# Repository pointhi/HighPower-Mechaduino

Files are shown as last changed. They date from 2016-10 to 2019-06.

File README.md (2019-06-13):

View this project on [CADLAB.io](https://cadlab.io/project/1867). 

# HighPower-Mechaduino

KiCad based Mechaduino derivative which drives up to 10A.

This is the original Meachaduino Project: https://hackaday.io/project/11224-mechaduino

**Warning: This Board is currently under development. Simply fabricating it doesn't mean it would work!**
See [v0.1_BUILD_LOG.md](https://github.com/pointhi/HighPower-Mechaduino/blob/master/v0.1_BUILD_LOG.md) for some problems
found while building the first prototype.

A big thanks to the [Shuttleworth Foundation](https://shuttleworthfoundation.org) for supporting the development of this Project.

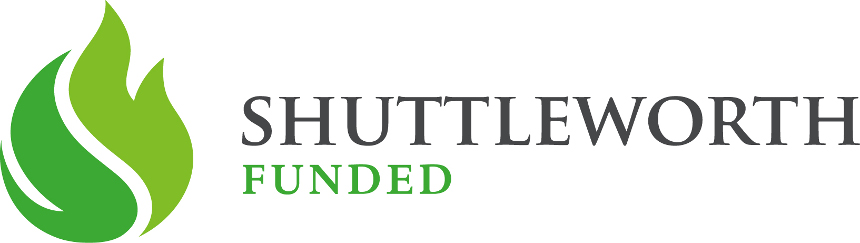
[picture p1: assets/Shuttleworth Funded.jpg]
Shuttleworth Funded


### Improvements

* ESD protection (especially USB)
* flyback diodes
* stronger drivers
* better silkscreen
* correct use of blocking capacitors
* fuse (for protection against polarity reversal and shorts)
* input voltage measurement
* supply of the microcontroller via the motor voltage supply
* external storage for calibration and configuration data
* Temperature sensor

### Planned Electrical/Mechanical Ratings

* Input Voltage-range of about 12V-50V
* N-Mosfet Driver which is capable of about 10A
* board in the size of NEMA 23 (56x56xmm) or NEMA 24 (60x60mm)

### Interfaces

* USB
* UART (3.3V)
* Step/Dir/Enable (PoStep25-32 Compatible)

### various informations

* [BOM](https://rawgit.com/pointhi/HighPower-Mechaduino/master/pcb/HighPower-Mechaduino.html) can be created using [KiBoM](https://github.com/SchrodingersGat/KiBoM)
* There exists a modified version of the Firmware for this project: [ElektronikNode/Mechaduino-Firmware](https://github.com/ElektronikNode/Mechaduino-Firmware)

## License

Hardware including documentation is licensed under [CERN OHL v.1.2. license](http://www.ohwr.org/licenses/cern-ohl/v1.2)

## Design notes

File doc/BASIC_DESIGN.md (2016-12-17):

## Basic Design

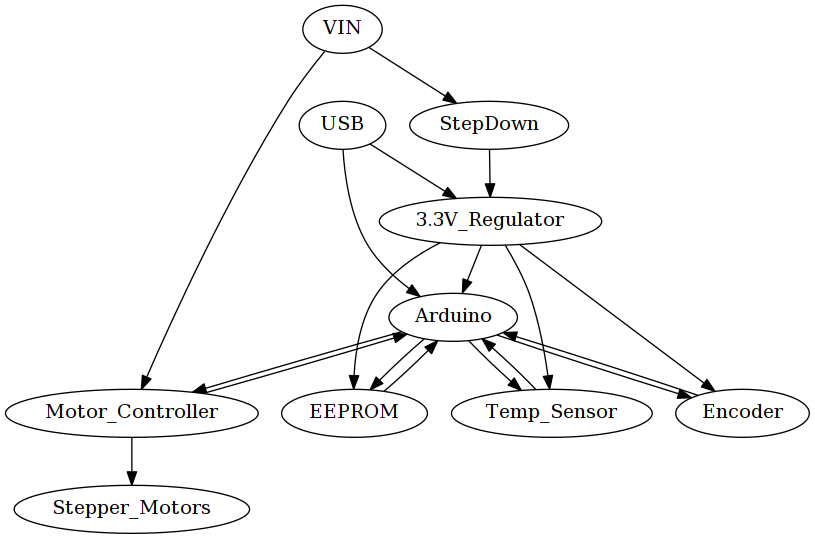
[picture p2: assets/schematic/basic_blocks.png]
Basic Blocks


#### Step Down

Converts VIN to about 5V

#### 3.3V Regulator

Converts the 5V coming from the Step Down, or otherwise coming from the USB input to 3.3V

#### Arduino Zero

Based on the Arduino Zero schematic

#### Encoder

#### Motor Controller

#### EEPROM

We have a 64kBit EEPROM, to store the calibration data in a persistent way (Otherwise it would be overwritten when flashing a new firmware).

We cannot store the calibration data in a simple key-value form which would require 2^14 values with 0.01° resolution. Because of that we need to store this table using compression algorithms.

Here is the idea of a simple compression algorithm, by storing the relative change of degree instead of an absolute position. We assume the values are monotonically increasing:

> Every relative change is stored by a ```0```, followed by a specific amount of ```1``` Bits defining the offset to the previous value in 0.01° accuray. When we assume we have to map 360° on 0.01° accuray, using a sensor with 14bit accuray, we would need a table with the size of ```2^14+360*100 = 52384``` Bits which can be stored in a 64kBit EEPROM.

When we look onto the calibration routine, and using the informations about the algorithm used, we could probably further decrease the amount of data required to store the table.

#### Temperature Sensor

We have an I²C temperatur sensor on the pcb, to get the temperatur of the driver mosfets. There is furthermore a extension connector where we can attach two 1-Wire temperatur sensors to get the motor temperatur (or any other informations which could be usefull).

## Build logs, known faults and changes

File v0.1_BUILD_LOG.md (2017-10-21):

## PCB Assembly of first Prototype (v0.1) (18.03.2017)

### Assembly Order

1. Driver Mosfets, using a heating plate
2. Driver IC
3. SAMD21 ARM CPU
3. Chip SMD Capacitors
4. Chip SMD Resistors
5. Diodes
6. Fuses
7. Inductors
8. Remainig MosFET
9. Some IC's on the top side (regulator, temp-sensor)
10. Crystal
11. Switch
12. USB and SWD connector
13. Electrolyth Capacitors
14. Remaining Connectors
15. U1 and U3

required time for soldering: 4:30h

Top                                                             | Bottom
:--------------------------------------------------------------:|:-------------------------------------------------------------------:
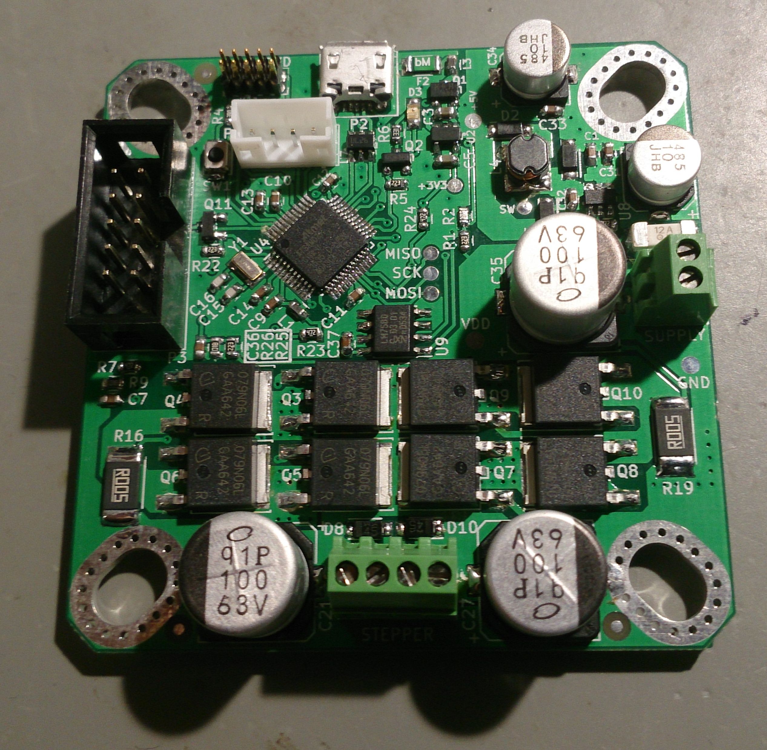
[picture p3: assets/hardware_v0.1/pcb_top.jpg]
Top side of assembled PCB
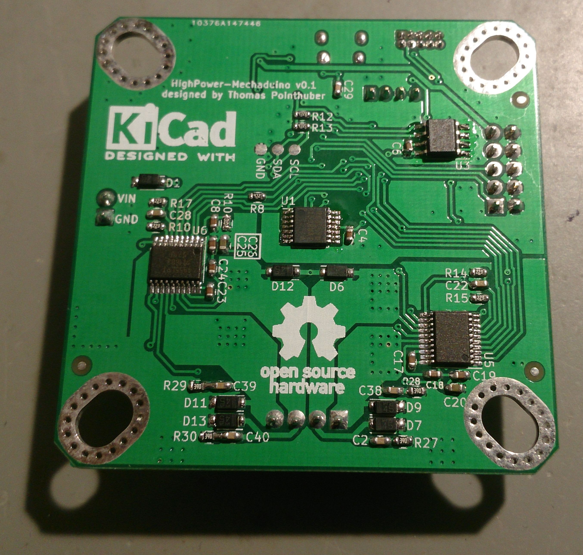
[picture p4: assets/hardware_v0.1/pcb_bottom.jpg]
Bottom side of assembled PCB
  | 

### Problems found while Assembly

* R10 and R18 looks quite similar on pcb (via below silkscreen)
* A bit more thermal spaces to the pad's would be useful
* switch is note easy to reach

## First tests of the prototype

### Step Down measurements

The only connection to the board was the Supply voltage connected to the SUPPLY connector.

V_in    | I_in      | TP 5V     | TP 3.3V
--------|-----------|-----------|--------
4.3V    | 2.1mA     | 4.0V      | 3.33V
5.0V    | 2.3mA     | 4.5V      | 3.33V
6.0V    | 2.2mA     | 4.5V      | 3.33V
7.0V    | 2.2mA     | 4.5V      | 3.33V
10.0V   | 1.9mA     | 4.6V      | 3.33V
12.0V   | 2.0mA     | 4.6V      | 3.33V
15.0V   | 2.2mA     | 4.6V      | 3.33V
20.0V   | 2.4mA     | 4.6V      | 3.33V
25.0V   | 2.6mA     | 4.6V      | 3.33V
30.0V   | 2.8mA     | 4.6V      | 3.33V
35.0V   | 3.1mA     | 4.6V      | 3.33V
40.0V   | 3.5mA     | 4.6V      | 3.33V
45.0V   | 3.8mA     | 4.6V      | 3.33V
48.0V   | 4.0mA     | 4.6V      | 3.33V
50.0V   | 4.2mA     | 4.6V      | 3.33V

For now, all seems OK. Please note, The 5V Test Point does not actually reach 5V. According to my calculations,
a voltage between 4.47-4.62V is expected. This is due some design decisions, which result in lower part requirements.

Expected Voltage at TP 3.3V lies between 3.25-3.35, which Is also looks OK.

Note to myself: Also measure the voltage at A_IN

### Programming of Arduino Bootloader (25.03.2017)

I'm using an ```ARM-USB-OCD-H``` connected to board usin the ```ARM-JTAG-SWD``` adapter.
Furthermore, I connected the usb port to my computer, to power up the device.

Content of ```openocd_olimex.cfg```:

```
source [find interface/ftdi/olimex-arm-usb-ocd-h.cfg]
source [find interface/ftdi/olimex-arm-jtag-swd.cfg]

set CHIPNAME at91samd21g18
set ENDIAN little

source [find target/at91samdXX.cfg]
```

#### upload bootloader using openocd

```
$ openocd -f openocd_olimex.cfg
```

Note: ``$HOME`` has to be replaced by actual path. Depending on library version, the path to the bootloader probably
also needs to be adjusted.

```
$ telnet 127.0.0.1 4444
> init
> halt
> at91samd bootloader 0
> program {{$HOME/.arduino15/packages/arduino/hardware/samd/1.6.12/bootloaders/zero/samd21_sam_ba.bin}} verify reset
> shutdown
```

When programming finished sucessfully, the LED (D3) should start slowly blinking, indicating that the bootloader is running.

### Upload first example using Arduino IDE

* Select ```Arduino/Genuino Zero (Native USB Port)``` as Boad
* Load the Blink Example
* Select Port which is opened by bootloaders
* press upload and wait until console finished

Now the status LED (D3) should blinking as expected

### Test Board Peripherie

I build a little programm which run's the stepper motor in half step mode.

To specify a maximum current for the motor driver, it was required to rewrite ```analogWrite(uint32_t pin, uint32_t value)```
to use a prescaler of 1/4 instead of 1/256, otherwise the analog output voltage wouldn't be very stable.

After some coding, this is now working, and was able to run a stepper motor with about 120 RPM and active overcurrent protection
using this driver pcb, showing that the general electronic is working as expected.

As next step, I will test the other circuit parts like the analog inputs as well as the SPI Magnetic Rotary Position Sensor,
I2C temperatur sensor and the I2C EEPROM.

### Problems found while Testing

* Pin 2 <-> Pin 4 are swapped on the schematic (they are also swapped in the original arduino schematic, and I didn't spot that)
* The SLEEPn description in the datasheet actually represents physical voltage, which means we need to manually wire
it to 5V to activate the controller

### Get Mechaduino Firmware running (21.10.2017)

We now have a modified mechaduino firmware for our version: [ElektronikNode/Mechaduino-Firmware](https://github.com/ElektronikNode/Mechaduino-Firmware)

I programmed the modified firmware, and it seems like all original features are working as expected. The Firmware still
lacks modifications to get the new features supported, but the basic systems seems to work like original Mechaduino.

## Search for errors

### Find MOSFET Driver failure

* Check for activated overcurrent protection of Motor Driver
* Measure if there is a short on a MOSFET
* Measure H-Bridge output voltage, it should be clearly at a voltage of 0V or Vin
* Measure Gate Driver Voltage. Should be either 0V or something between 6.5-7.5V (changes if the MOSFET is driven or not)

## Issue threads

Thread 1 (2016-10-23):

Current rating

SloMusti, 2016-10-23:
I believe 6A current rating at 48V is completely sufficient for most applications the board would be used with NEMA 23 motors.

pointhi, 2016-10-23:
I also think so. But the dimension for 10A does requires only minimal changes (I have to define the current sensing a bit wider).

If the finished board can drive 10A permanently has to be tested. I think it's I think mostly defined how wide I can make the copper lines and if the Capacitors are big enough designed. But to have the possibility to drive some peak doesn't sound like a bad idea.

3eggert, 2019-01-15:
In the datasheet is written:
Accurate angle measurements of around ±2° ... 4° after calibration at room temperature
seems not usable for this application to me

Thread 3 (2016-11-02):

Consider using RPi Zero

SloMusti, 2016-11-02:
Based on the 4EUR cost, RPi zero may be a very good choice: https://www.raspberrypi.org/products/pi-zero/ please consider that.

pointhi, 2016-11-02:
I don't think so.

One problem is we would then likely run an OS, which could conflict with the tight Real time requirements such a controller has. Another problem is that RPI zero is not usable for projects which required bigger quantities of them, because they are normally limited to 1 pice per customer.

SloMusti, 2016-11-02:
Regarding supply-chain the volumes will likely be greater after a while. Please check if of if not real time algorithms can be built on RPi zero, hopefully someone wrote about this.

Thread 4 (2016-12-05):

Shunt Resistors

feichtinger, 2016-12-05:
I think a resistor with 4-wire-connection should be used for the shunt resistors R16 and R19. Otherwise the load current flowing throw the groundplane could lead to a wrong current feedback due to the parasitic resistance and inductance.

The connection on the drain side is already (almost) correct, but not so on the ground plane.

pointhi, 2016-12-08:
unfortunately, our motor controller doesn't support such types of shunts. Probably we could arrange the tracks a bit to minify voltage drops as much as possible.

Closed 2017-02-04.

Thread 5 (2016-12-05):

Free Wheeling Diodes

feichtinger, 2016-12-05:
The free wheeling diodes D6-D9 and D10-D13 are schottky diodes so the appropriate symbol should be used.

Also the lower diodes should be connected to the MOSFET-drains instead of GND if possible.

pointhi, 2016-12-08:
Connecting the Diodes directly to GND simplify pcb layout, and shouldn't lead to big issues on the functional side

Closed 2016-12-08.

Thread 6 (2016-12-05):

Current Reference VREF

feichtinger, 2016-12-05:
The text saying "I_MAX=14"next to the voltage dividers for VREF (R7-R10) is wrong. Instead it is 11.6A.

U2 = U1*R2/(R1+R2) != U1*R2/R1
;)

Also I think that the cutoff frequency of the low pass should be a bit higher. With R9, R10=1k and C7, C8=100n the cutoff frequency is ~1.5 kHz.

For a 200 steps/rev motor turning with 2000 RPM (which is not too unrealistic I think) the step frequency (in our case: sine frequency) would be 6667 Hz. I would suggest to set C7 and C8 to 10nF instead of 100nF.

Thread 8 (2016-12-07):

step down converter MCP16331

feichtinger, 2016-12-07:
The collector of the bootstrap diode D5 should be connected to the BOOST pin an not to the SW pin! See the example circuit on page 2 in the datasheet.

Also I think that the output diode D2 should be directly in series with the induction L4. Otherwise the output voltage could drop due to a transient load current. This could also cause stability problems of the voltage regulator.

Closed 2017-02-11.

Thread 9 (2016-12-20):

price optimizations

pointhi, 2016-12-20:
The current component price range is about 50-60€ per board (when buying for 10 pbc's). Not problematic for the prototype board, but we should optimize it.

This is a list of the most expensive parts of the board (based on the discounts you get when you buy for about 10 boards):

Component             | price per board | description
-------------------------|---------------------|-----
AS5047D                | 8,19€ | encoder
IPD079N06L3         | 5,90€ | motor driver mosfets
ATSAMD21G18A    | 4,78€ | controller
A4955GLPTR         | 2,84€ | motor controller
RB162MM-60CT    | 2,11€ | schottky diodes
744773122             | 1,96€ | inductor for step down
10UF POLY ELCO  | 1,83€ | elco for step down (very low esr)
TERM BLOCK 4POS | 1,67€ | step down connector
MCP16331T | 1,26€ | step down regulator

those few (main) components sum up to about 30,54€ per board.

gamerpaddy, 2017-04-09:
Can this software run on 328p, stm32f103, or other lower cost, more available processors?

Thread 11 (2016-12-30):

5V USB power switch

VojislavM, 2016-12-30:
Maybe it would be beater to change the switch part, so the MOSFET Q1 should be triggered by the USB and not the VDD. I think it would be beater this way because the USB voltage is constant, +5V, and VDD is not, it can be from 12V to 50V, and the gate current would not be the same. See the reference picture:

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

pointhi, 2017-01-07:
A possible problem with this approach is the USB Voltage, which could be as low as 4.5V (by specification), and where the diode adds additional 0.3-0.6V drop. Means about 4V at the output side.

No problem for my internal circuit, and I hope the same goes for your circuit on the ProStep Connector. But we should clarify specification first.

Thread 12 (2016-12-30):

MCP16331_5V circuit

VojislavM, 2016-12-30:
Check the [datasheet](http://ww1.microchip.com/downloads/en/DeviceDoc/20005308B.pdf) for the reference circuit. If you change the schematic like in #11, you can lose the D2 diode. Otherwise move the resistors R20 and R21 in front of the diode D2.

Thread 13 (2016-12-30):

programming header P1

VojislavM, 2016-12-30:
On the programming header P1 the pin 7 is connected to the ground, and in the Arduino zero [schematic](https://www.arduino.cc/en/uploads/Main/ArduinoZero-schematic.pdf) it is not. I know this is not a big deal, but maybe (in some parallel universe) it could bother the programator when connected.

pointhi, 2017-01-07:
@VojislavM , thanks for spotting this

Just for documentation (from atmel website):

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

Closed 2017-01-07.

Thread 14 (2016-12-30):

magnetic encoder option TLV493D

VojislavM, 2016-12-30:
Regarding enhancements mentioned in the #9 issue, possible option for magnetic encoder is [TLV493D](http://www.infineon.com/cms/en/product/sensor/magnetic-position-sensor/3d-magnetic-sensor/TLV493D-A1B6/productType.html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) which is ~ [1 EUR](http://hr.mouser.com/ProductDetail/Infineon-Technologies/TLV493DA1B6HTSA2/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). There is even a small dev kit for it [TLV493D-A1B6 2 GO KIT](http://www.infineon.com/cms/en/product/sensor/magnetic-position-sensor/3d-magnetic-sensor/TLV493D-A1B6+2+GO+KIT/productType.html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)

pointhi, 2017-01-07:
looks interesting. I will build the prototype with the current one, but we can do some evaluations with other sensors like this one. But I don't have a idea how good this sensor would behave in our conditions (3-Axis general sensor vs 1-Axis sensor especially for absolute positioning of motors).

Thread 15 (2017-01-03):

pcb mounting holes

feichtinger, 2017-01-03:
I started to design a housing/mounting for the HighPower-Mechaduino on a NEMA24 stepper motor and discovered that the mounting holes in the PCB are made for M4 only while they are for M5 in the motor. See this screenshot:
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

(The CAD model is based on measurements form an actual motor.)

See also this datasheet of a NEMA 23 motor:
http://www.omc-stepperonline.com/download/pdf/23HS16-0884S.pdf

I think it would be good to change mounting holes in the pcb to fit to M5 screws (a diameter of 5.2mm should be sufficient)

There might be some NEMA23/24 motors where the mounting holes are actually M4, but it is easier to fit an M4 screw into an M5 hole than the other way round. ;)

pointhi, 2017-02-04:
fixed: fba158e134bf2179033e19b4fcdc3ea2f984c09f

Closed 2017-02-04.

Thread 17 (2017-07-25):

Have you tested the board?

mzarnowski, 2017-07-25:
Hi,
Tried to find any contact info to send you a private message, but couldn't find any thus I'm writing this post.

Have you managed to test current layout of the board? I'm in need of such controller and just wondered if it's working or are there any serious issues that you're aware of?

Let me know if I can help in further development.

Cheers,
Maciej

pointhi, 2017-07-25:
I have some documentation about the first prototype which should give you a good overview of the current status:

https://github.com/pointhi/HighPower-Mechaduino/blob/master/v0.1_BUILD_LOG.md

I found some little layout problems. One is a missing connection which was fixed with some wire on the prototype, the other one were swapped pins in the schematic which didn't correspondent with the arduino pin names.

We started running a modfiied Mechaduino Firmware a few days ago, and it looks good for now. But there seems to be some communication issue with USB, which is not resolved yet (The calibration table given by the firmware has missing values)

radu103, 2018-03-01:
Is it working now ?

pointhi, 2018-03-03:
No fixes for the PCB were pushed to the repo at the moment. The Prototype works so far, but has some weird behaviour between the two output drivers. Hopefully only a partly hardware defect of a MosFet.

The software runs to the extend to have single stepping, constant velocity, constant tor queue successfully working to some extend.

3eggert, 2019-01-15:
Is there still development happening? If not, where there blocking problems or did it only loose importance?

pointhi, 2019-01-16:
we built a second prototype which has the same stepping behavior. Our current assumption is that it is a problem with the current limiters of the two H-Bridges which causes different current-limits to be enforced.

There is still interest in completing the project, but until the issues are solved for full/half-step operation the system is not really ready in my point of view. Unfortunately, I don't have too much time to work on it as well (and other projects as well)

Bastler100, 2019-06-09:
Hallo pointhi,
ich würde mir gerne so einen High-Power-Mechaduino nachbauen. Gibt es eine Version von der Du weißt das sie funktioniert? Hardware und Firmware?  Bei meinen Selbstbauversuchen von Fräsmaschinen habe ich immer in einer Achse Schrittverluste, die will ich in den Griff bekommen.
Vielen Dank für deine Antwort
Hans

pointhi, 2019-06-11:
@Bastler100 no progress so far. Using it only to prevent step losses should work, but the hardware still does not work as seamlessly as I would like. Furthermore, the pcb still misses the bugfixes.

Bastler100, 2019-06-12:
Hallo Thomas,danke für deine Antwort. Ich will dir nicht auf den Wecker gehen, aber eine Frage:Wäre ein Lösungsansatz für einen stärkeren Controller nicht den Motortreiber
gegen einen eingangssignalkompatiblen Motortreiber oder Gatetreiber
auszutauschen? Dann könnte man doch die Software unverändert verwenden?Vielen Dank für deine Antwort Hans

-----Ursprüngliche Mitteilung-----
Von: Thomas Pointhuber <notifications@github.com>
An: pointhi/HighPower-Mechaduino <HighPower-Mechaduino@noreply.github.com>
Cc: Bastler100 <HaHoLang@aol.com>; Mention <mention@noreply.github.com>
Verschickt: Di, 11. Jun. 2019 8:59
Betreff: Re: [pointhi/HighPower-Mechaduino] Have you tested the board? (#17)

@Bastler100 no progress so far. Using it only to prevent step losses should work, but the hardware still does not work as seamlessly as I would like. Furthermore, the pcb still misses the bugfixes.—
You are receiving this because you were mentioned.
Reply to this email directly, view it on GitHub, or mute the thread.

pointhi, 2019-06-13:
changing the motor controller is definitly a solution for the problems. Ideally moving from two seperated H-bridges to one integrated motor controller which still allows us to controll currents of both H-bridges separatly.

pointhi, 2019-06-13:
This controller could work: https://www.allegromicro.com/en/Products/Motor-Driver-And-Interface-ICs/Bipolar-Stepper-Motor-Drivers/A3985.aspx

One advantage is that the current is set via internal DAC (no longer disturbances due to analog lines from mcu -> motor controller including ground lines back

Would be nice to add a list of possible controllers

pointhi, 2019-06-13:
Another alternative: https://www.trinamic.com/products/integrated-circuits/details/tmc5160/

Advantage would be that we could offload calculation requirements to the controller because it already handles most of the stuff itself. Disadvantage is that we cannot directly control the current anymore per line, but we get a good control-loop instead.

Bastler100, 2019-06-13:
Hallo Thomas,danke für deine Antwort. Mein Plan war, zuerst die Außenmaße der Platine auf ca 60 x 60mmpassend zu NEMA23 Motore zu vergrössern und anstatt des A4954 Motortreibers zwei A4950
Motortreiber zu benutzen. Die wären ja Ein- und Ausgangssignalkompatibel und müssten vonder Stromstärke für die 23er ausreichen. Sollte das funktionieren würde ich die Platine für die
NEMA34 bzw 42 vergrössern und als Motortreiber den DRV8402 nehmen.
MfG
 Hans

-----Ursprüngliche Mitteilung-----
Von: Thomas Pointhuber <notifications@github.com>
An: pointhi/HighPower-Mechaduino <HighPower-Mechaduino@noreply.github.com>
Cc: Bastler100 <HaHoLang@aol.com>; Mention <mention@noreply.github.com>
Verschickt: Do, 13. Jun. 2019 11:39
Betreff: Re: [pointhi/HighPower-Mechaduino] Have you tested the board? (#17)

Another alternative: https://www.trinamic.com/products/integrated-circuits/details/tmc5160/Advantage would be that we could offload calculation requirements to the controller because it already handles most of the stuff itself. Disadvantage is that we cannot directly control the current anymore per line, but we get a good control-loop instead.—
You are receiving this because you were mentioned.
Reply to this email directly, view it on GitHub, or mute the thread.

pointhi, 2019-06-13:
I created a wiki page to collect possible solutions: https://github.com/pointhi/HighPower-Mechaduino/wiki

annhan, 2020-04-03:
any update for this project

pointhi, 2020-04-04:
@annhan no updates for now.

WesleyBuck, 2020-05-11:
@pointhi Is there anyway we can assist in getting the project moving along?

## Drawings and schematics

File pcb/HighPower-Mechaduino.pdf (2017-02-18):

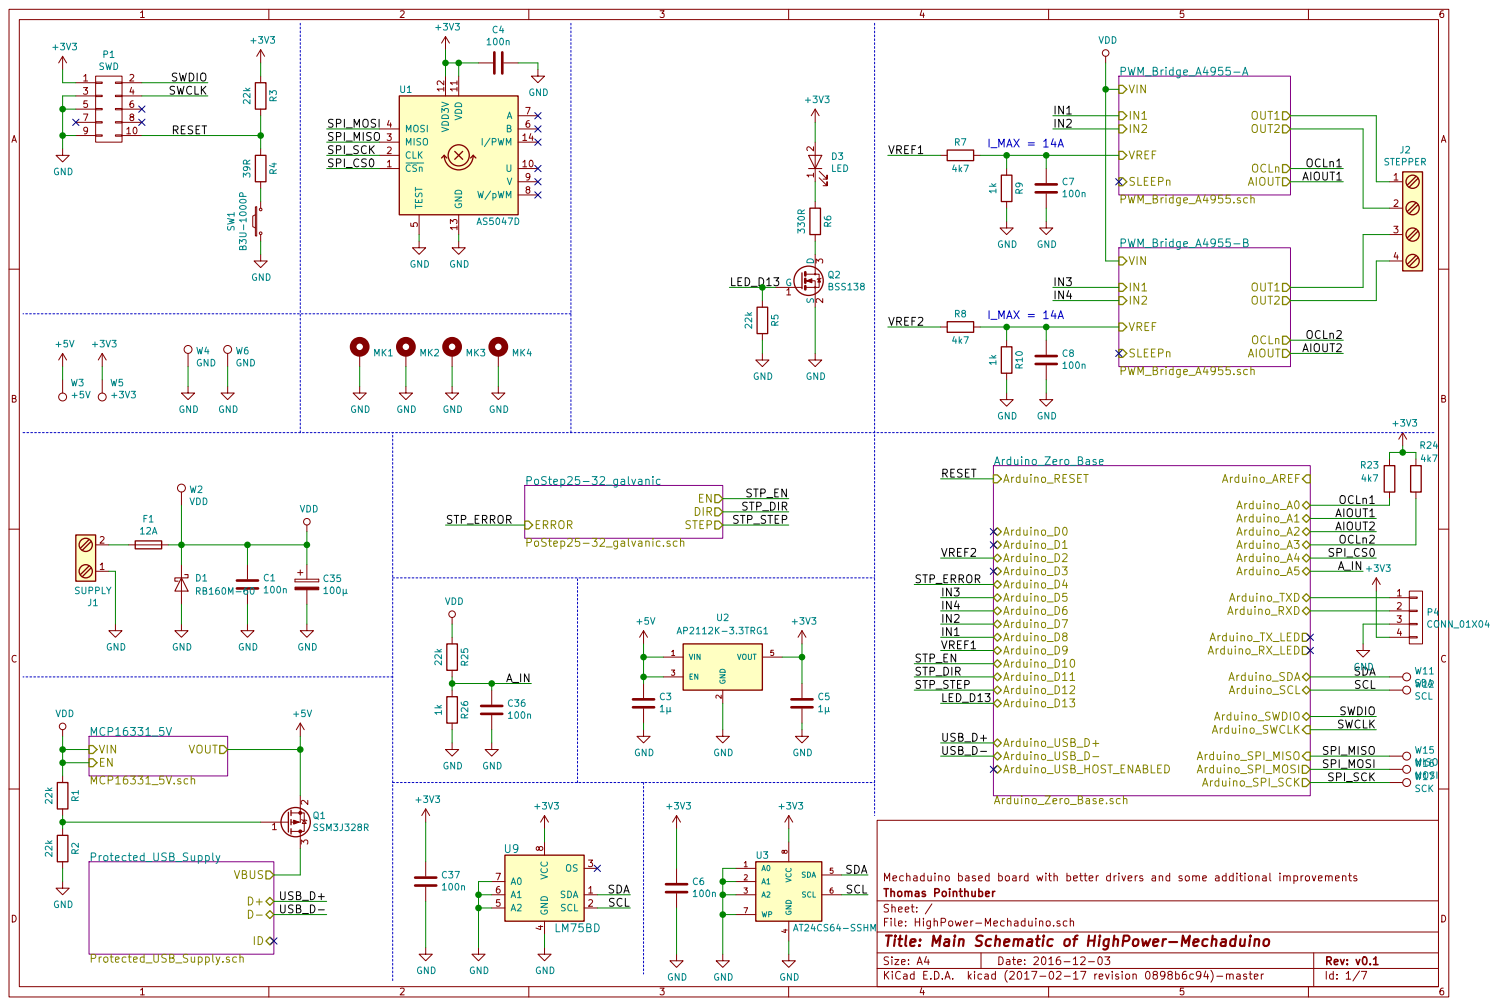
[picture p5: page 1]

STP_DIR
STP_STEP

AIOUT1

IN4 | 2
IN2 | 3

2 EN 3 VOUT 5 U2 AP2112K-3.3TRG1 GND GND
+5V GND

4 SDA 5 SCL 6 WP 7 VCC

SDA
File: HighPower-Mechaduino.sch Sheet: / Thomas Pointhuber Mechaduino based board with better drivers and some additional improvements

Id: 1/7 Title: Main Schematic of HighPower-Mechaduino

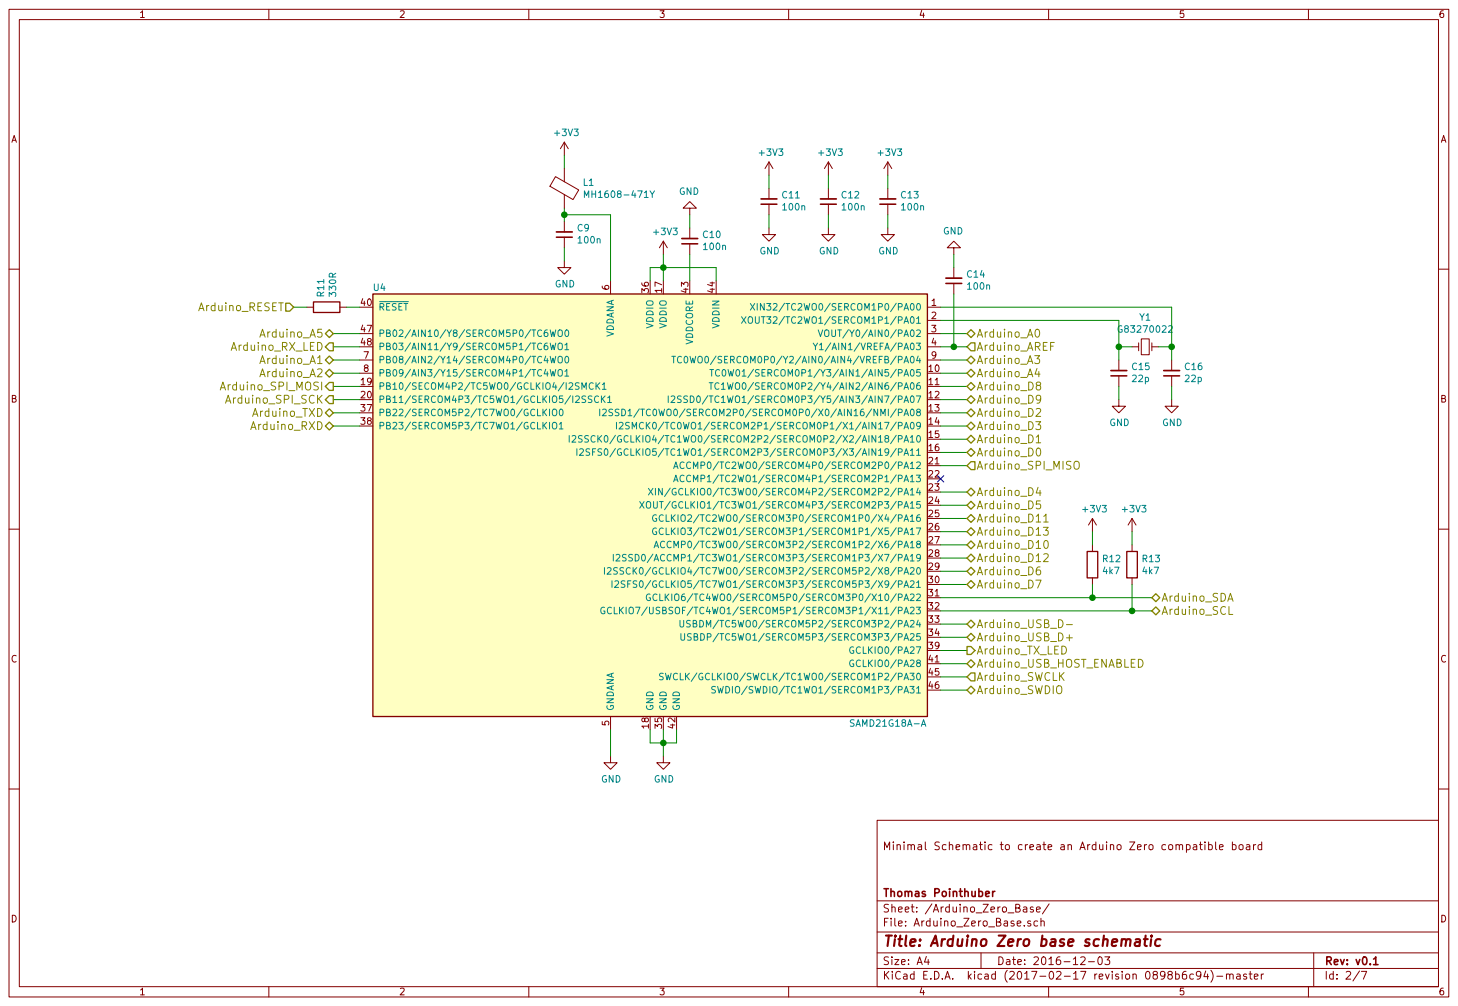
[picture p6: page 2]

File: Arduino_Zero_Base.sch
Id: 2/7 Title: Arduino Zero base schematic

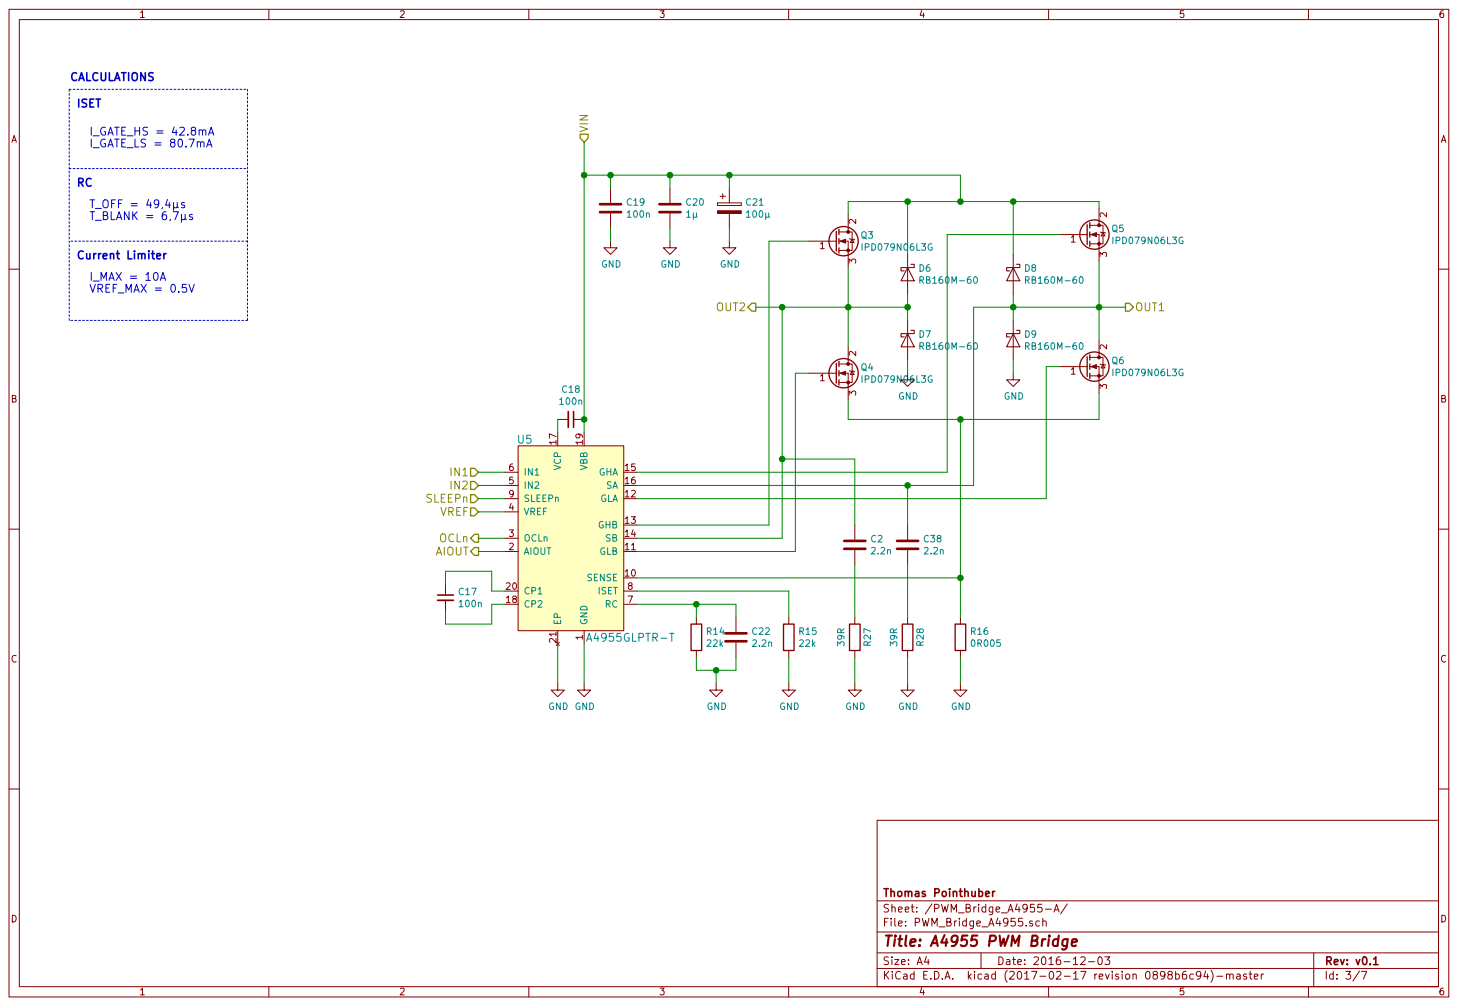
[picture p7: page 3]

Sheet: /PWM_Bridge_A4955-A/ Thomas Pointhuber GND

File: PWM_Bridge_A4955.sch
Id: 3/7 Title: A4955 PWM Bridge

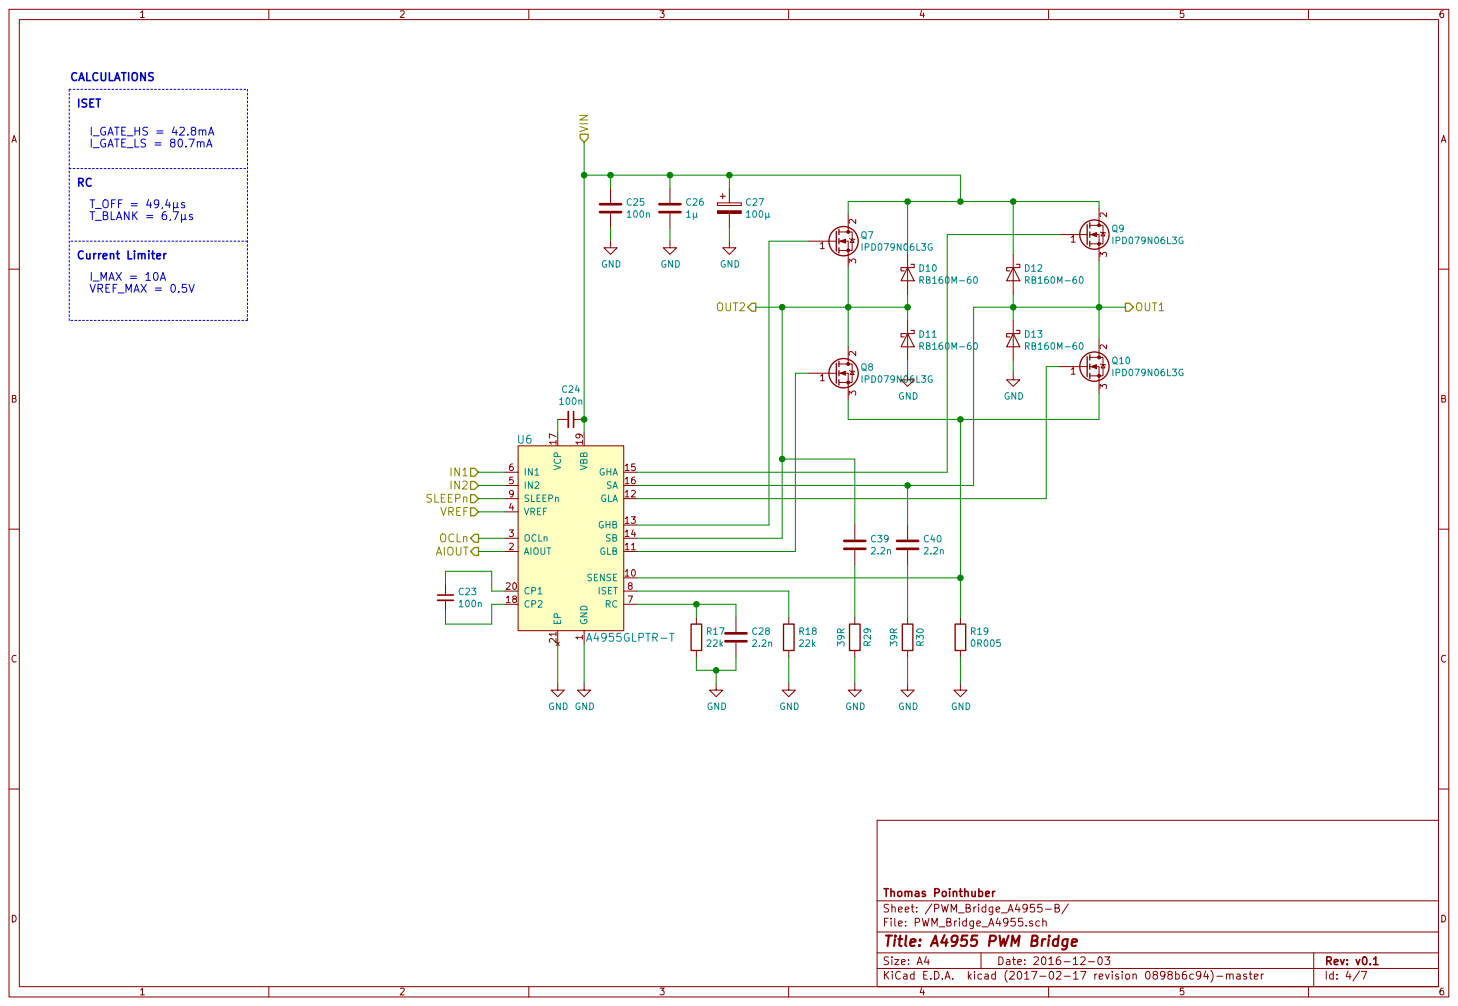
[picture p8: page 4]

Sheet: /PWM_Bridge_A4955-B/ Thomas Pointhuber GND

File: PWM_Bridge_A4955.sch
Id: 4/7 Title: A4955 PWM Bridge

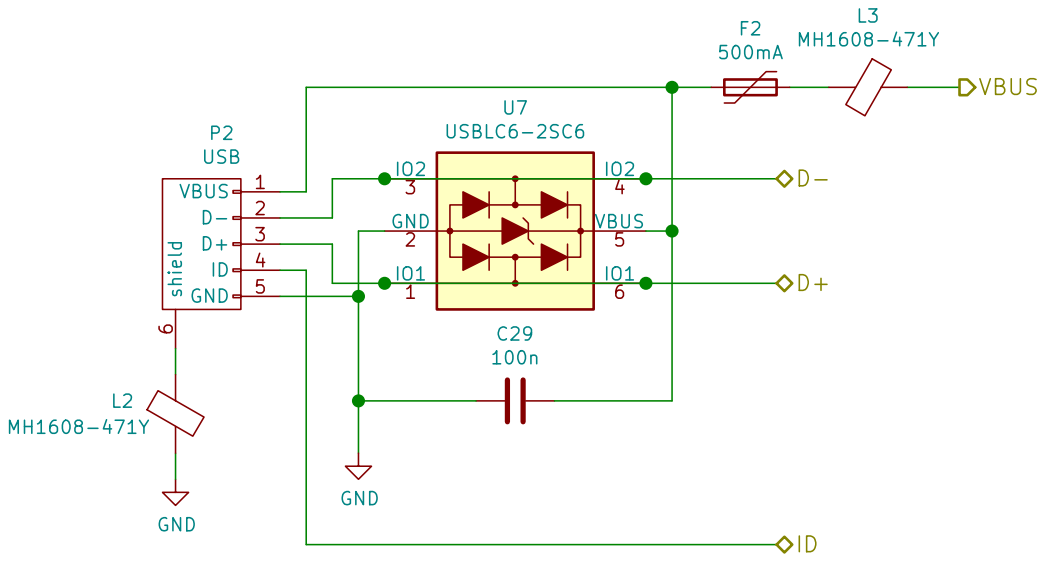
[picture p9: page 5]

File: Protected_USB_Supply.sch
Id: 5/7 Title: USB input including protection circuit

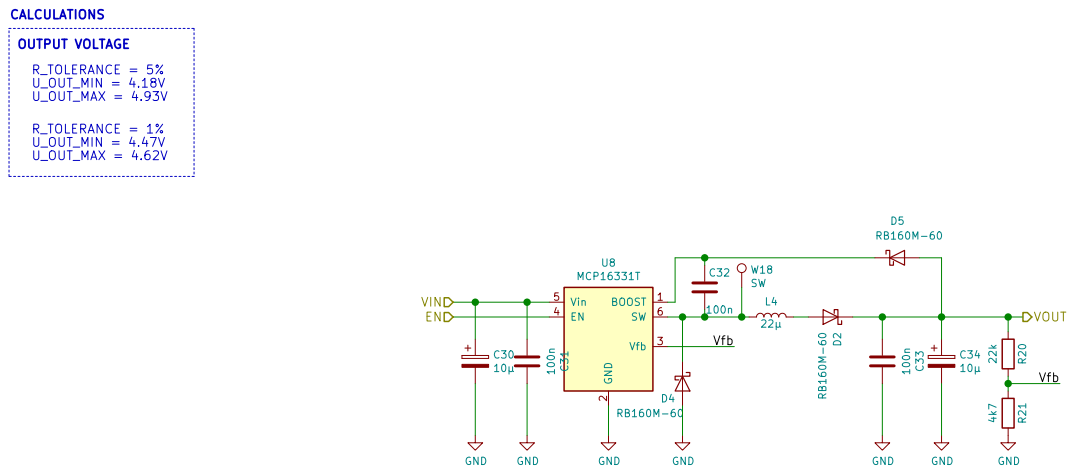
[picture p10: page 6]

2 Vfb 3 EN 4 Vin 5 SW 6 U8 MCP16331T GND

File: MCP16331_5V.sch
Id: 6/7 Title: Step Down with input range of 10V-50V

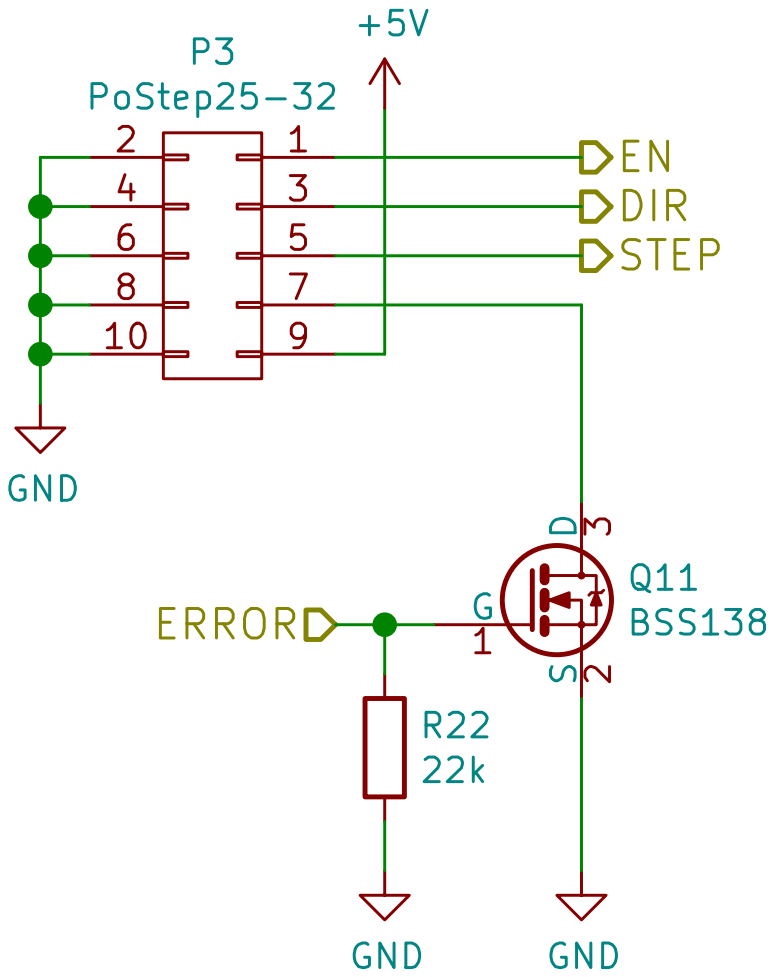
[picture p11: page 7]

File: PoStep25-32_galvanic.sch
Id: 7/7 Title: ProStep25-32 input including optional galvanic separation

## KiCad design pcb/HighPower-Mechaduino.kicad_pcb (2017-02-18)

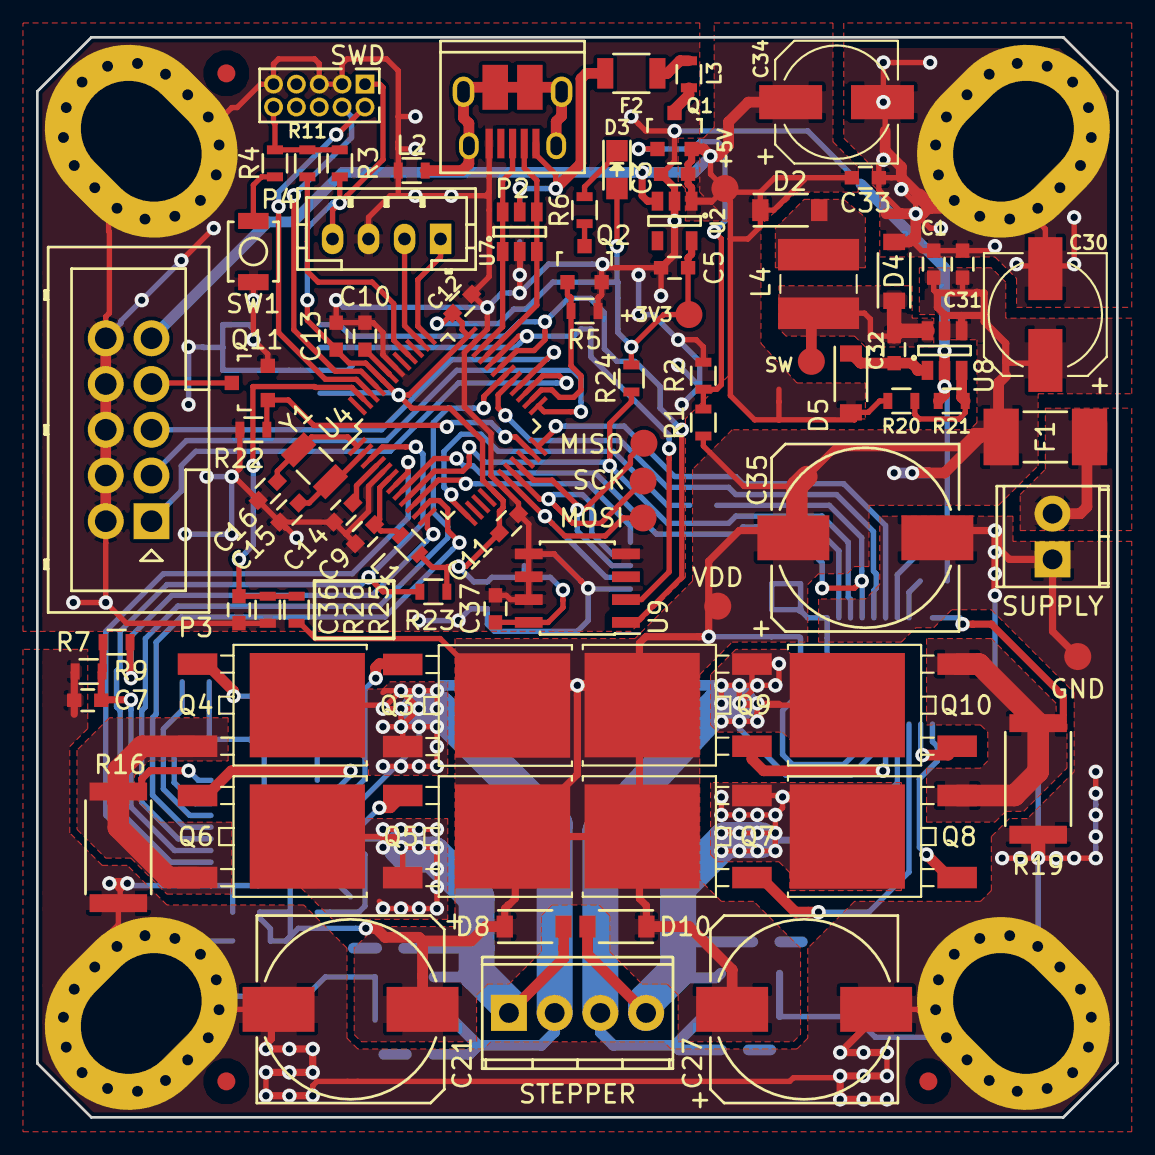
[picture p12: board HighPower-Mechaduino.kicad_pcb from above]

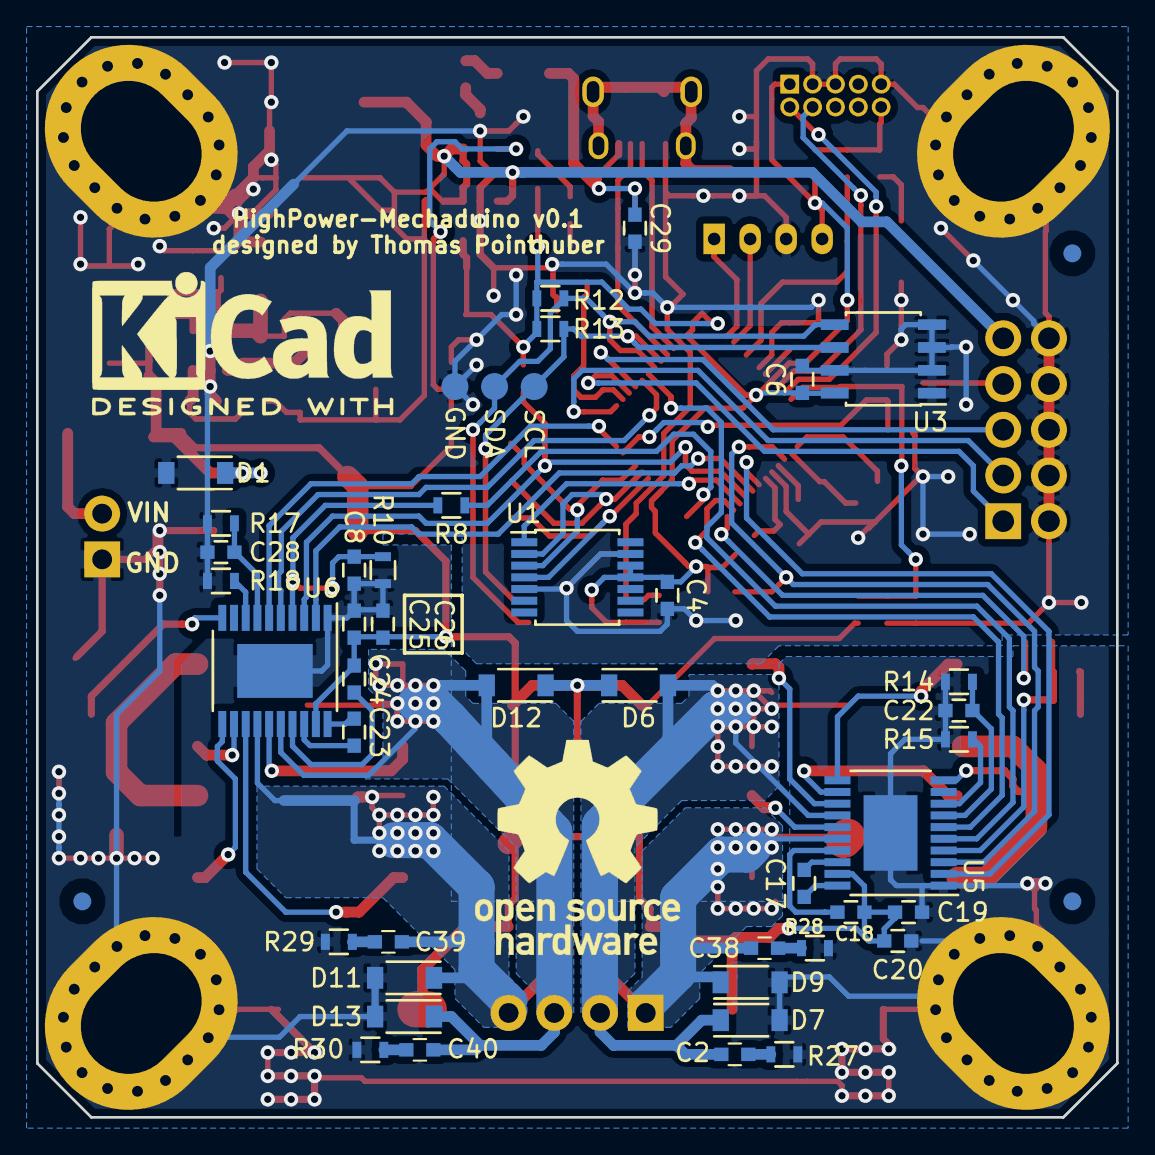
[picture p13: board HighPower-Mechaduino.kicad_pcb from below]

Board: 2 copper layers, 60.0 x 60.0 mm, 132 parts (44 on the bottom side), 83 nets.

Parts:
C1, C4, C6, C7, C8, C9, C10, C11, C12, C13, C14, C17, C18, C19, C23, C24, C25, C29, C31, C32, C33, C36, C37: 100n; C_0603
C2, C22, C28, C38, C39, C40: 2.2n; C_0603
C3, C5, C20, C26: 1µ; C_0603
C15, C16: 22p; C_0603
C21, C27, C35: 100µ; c_elec_10x10
C30, C34: 10µ; c_elec_6.6x5.8
D1, D2, D4, D5, D6, D7, D8, D9, D10, D11, D12, D13: RB160M-60; SOD-123
D3: LED; LED_0805
F1: 12A; Fuse_0679H
F2: 500mA; R_1206
J1: SUPPLY; TerminalBlock_Pheonix_MPT-2.54mm_2pol
J2: STEPPER; TerminalBlock_Pheonix_MPT-2.54mm_4pol
L1, L2, L3: MH1608-471Y; R_0603
L4: 22µ; Inductor_Würth_WE-PD2_4532
MK1, MK2, MK3, MK4: Mounting_Hole_PAD; MountingHole_5.3x7.3mm_M5_Pad_Via
P1: SWD; Pin_Header_Straight_2x05_Pitch1.27mm
P2: USB; USB_Micro-B_10103594-0001LF
P3: PoStep25-32; On-Shore-Technology_ED1543_2x05x2.54mm_Straight
P4: CONN_01X04; JST_PH_B4B-PH-K_04x2.00mm_Straight
Q1: SSM3J328R; SOT-23
Q2, Q11: BSS138; SOT-23
Q3, Q4, Q5, Q6, Q7, Q8, Q9, Q10: IPD079N06L3G; PG-TO-252-3-313
R1, R2, R3, R5, R14, R15, R17, R18, R20, R22, R25: 22k; R_0603
R4, R27, R28, R29, R30: 39R; R_0603
R6, R11: 330R; R_0603
R7, R8, R12, R13, R21, R23, R24: 4k7; R_0603
R9, R10, R26: 1k; R_0603
R16, R19: 0R005; R_2512
SW1: B3U-1000P; SW_SPST_B3U-1000P
U1: AS5047D; TSSOP-14_4.4x5mm_Pitch0.65mm
U2: AP2112K-3.3TRG1; SOT-23-5
U3: AT24CS64-SSHM; SOIC-8_3.9x4.9mm_Pitch1.27mm
U4: SAMD21G18A-A; TQFP-48_7x7mm_Pitch0.5mm
U5, U6: A4955GLPTR-T; ETSSOP-20-1EP_4.4x6.5mm_Pitch0.65mm
U7: USBLC6-2SC6; SOT-23-6
U8: MCP16331T; SOT-23-6
U9: LM75BD; SOIC-8_3.9x4.9mm_Pitch1.27mm
W2: VDD; Measurement_Point_Round-SMD-Pad_Small
W3: +5V; Measurement_Point_Round-SMD-Pad_Small
W4, W6: GND; Measurement_Point_Round-SMD-Pad_Small
W5: +3V3; Measurement_Point_Round-SMD-Pad_Small
W11: SDA; Measurement_Point_Round-SMD-Pad_Small
W12: SCL; Measurement_Point_Round-SMD-Pad_Small
W15: MISO; Measurement_Point_Round-SMD-Pad_Small
W16: MOSI; Measurement_Point_Round-SMD-Pad_Small
W17: SCK; Measurement_Point_Round-SMD-Pad_Small
W18: SW; Measurement_Point_Round-SMD-Pad_Small
Y1: G83270022; Crystal_SMD_G8

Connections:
+3V3: C4.2, C5.2, C6.2, C11.2, C12.2, C13.2, C37.2, D3.2, L1.1, P1.1, P4.4, R3.2, R12.1, R13.1, R23.2, R24.2, U1.11, U1.12, U2.5, U3.8, U4.17, U4.36, U4.44, U9.8, W5.1
+5V: C3.2, C33.1, C34.1, D2.1, D5.2, P3.9, Q1.2, R20.2, U2.1, U2.3, W3.1
/AIOUT1: U4.7, U5.2
/AIOUT2: U4.8, U6.2
/A_IN: C36.2, R25.1, R26.2, U4.47
/Arduino_Zero_Base/Arduino_AREF: C14.1, U4.4
/Arduino_Zero_Base/Arduino_RXD: P4.2, U4.38
/Arduino_Zero_Base/Arduino_TXD: P4.1, U4.37
/IN1: U4.11, U5.6
/IN2: U4.30, U5.5
/IN3: U4.24, U6.6
/IN4: U4.29, U6.5
/LED_D13: Q2.1, R5.2, U4.26
/MCP16331_5V/Vfb: R20.1, R21.2, U8.3
/OCLn1: R23.1, U4.3, U5.3
/OCLn2: R24.1, U4.9, U6.3
/PWM_Bridge_A4955-A/OUT1: C38.1, D8.2, D9.1, J2.1, Q5.3, Q6.2, U5.16
/PWM_Bridge_A4955-A/OUT2: C2.1, D6.2, D7.1, J2.2, Q3.3, Q4.2, U5.14
/PWM_Bridge_A4955-A/VREF: C7.2, R7.1, R9.2, U5.4
/PWM_Bridge_A4955-B/OUT1: C40.1, D12.2, D13.1, J2.3, Q9.3, Q10.2, U6.16
/PWM_Bridge_A4955-B/OUT2: C39.1, D10.2, D11.1, J2.4, Q7.3, Q8.2, U6.14
/PWM_Bridge_A4955-B/VREF: C8.2, R8.1, R10.2, U6.4
/Protected_USB_Supply/VBUS: L3.1, Q1.3
/RESET: P1.10, R3.1, R4.2, R11.1
/SCL: R13.2, U3.6, U4.32, U9.2, W12.1
/SDA: R12.2, U3.5, U4.31, U9.1, W11.1
/SPI_CS0: U1.1, U4.10
/SPI_MISO: U1.3, U4.21, W15.1
/SPI_MOSI: U1.4, U4.19, W16.1
/SPI_SCK: U1.2, U4.20, W17.1
/STP_DIR: P3.3, U4.25
/STP_EN: P3.1, U4.27
/STP_ERROR: Q11.1, R22.1, U4.23
/STP_STEP: P3.5, U4.28
/SWCLK: P1.4, U4.45
/SWDIO: P1.2, U4.46
/USB_D+: P2.3, U4.34, U7.1, U7.6
/USB_D-: P2.2, U4.33, U7.3, U7.4
/VREF1: R7.2, U4.12
/VREF2: R8.2, U4.13
GND: C1.1, C3.1, C4.1, C5.1, C6.1, C7.1, C8.1, C9.1, C10.2, C11.1, C12.1, C13.1, C14.2, C15.1, C16.1, C19.2, C20.2, C21.2, C22.2, C25.2, C26.2, C27.2, C28.2, C29.1, C30.2, C31.2, C33.2, C34.2, C35.2, C36.1, C37.1, D1.2, D4.2, D7.2, D9.2, D11.2, D13.2, J1.1, L2.2, MK1.1, MK2.1, MK3.1, MK4.1, P1.3, P1.5, P1.9, P2.5, P3.2, P3.4, P3.6, P3.8, P3.10, P4.3, Q2.2, Q11.2, R2.1, R5.1, R9.1, R10.1, R14.2, R15.2, R16.2, R17.2, R18.2, R19.2, R21.1, R22.2, R26.1, R27.1, R28.1, R29.1, R30.1, SW1.1, U1.5, U1.13, U2.2, U3.1, U3.2, U3.3, U3.4, U3.7, U4.5, U4.18, U4.35, U4.42, U5.1, U5.21, U6.1, U6.21, U7.2, U8.2, U9.4, U9.5, U9.6, U9.7, W4.1, W6.1
unnamed: C2.2, R27.2
unnamed: C9.2, L1.2, U4.6
unnamed: C10.1, U4.43
unnamed: C15.2, U4.2, Y1.1
unnamed: C16.2, U4.1, Y1.2
unnamed: C17.1, U5.20
unnamed: C17.2, U5.18
unnamed: C18.2, U5.17
unnamed: C22.1, R14.1, U5.7
unnamed: C23.1, U6.20
unnamed: C23.2, U6.18
unnamed: C24.2, U6.17
unnamed: C28.1, R17.1, U6.7
unnamed: C29.2, F2.2, P2.1, U7.5
unnamed: C32.1, D5.1, U8.1
unnamed: C32.2, D4.1, L4.1, U8.6, W18.1
unnamed: C38.2, R28.2
unnamed: C39.2, R29.2
unnamed: C40.2, R30.2
unnamed: D2.2, L4.2
unnamed: D3.1, R6.2
unnamed: F1.2, J1.2
unnamed: F2.1, L3.2
unnamed: L2.1, P2.6
unnamed: P3.7, Q11.3
unnamed: Q1.1, R1.1, R2.2
unnamed: Q2.3, R6.1
unnamed: Q3.1, U5.13
unnamed: Q4.1, U5.11
unnamed: Q4.3, Q6.3, R16.1, U5.10
unnamed: Q5.1, U5.15
unnamed: Q6.1, U5.12
unnamed: Q7.1, U6.13
unnamed: Q8.1, U6.11
unnamed: Q9.1, U6.15
unnamed: Q10.1, U6.12
unnamed: Q8.3, Q10.3, R19.1, U6.10
unnamed: R4.1, SW1.2
unnamed: R11.2, U4.40
unnamed: R15.1, U5.8
unnamed: R18.1, U6.8
VDD: C1.2, C18.1, C19.1, C20.1, C21.1, C24.1, C25.1, C26.1, C27.1, C30.1, C31.1, C35.1, D1.1, D6.1, D8.1, D10.1, D12.1, F1.1, Q3.2, Q5.2, Q7.2, Q9.2, R1.2, R25.2, U5.19, U6.19, U8.4, U8.5, W2.1

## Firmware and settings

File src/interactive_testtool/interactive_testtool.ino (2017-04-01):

#include <Arduino.h>

// First Driver module
#define DRIVER_IN1 8
#define DRIVER_IN2 7
#define DRIVER_VREF1 9
#define DRIVER_OCLn1 A0
#define DRIVER_AIOUT1 A1

// Second Driver module
#define DRIVER_IN3 5
#define DRIVER_IN4 6
#define DRIVER_VREF2 4
#define DRIVER_OCLn2 A3
#define DRIVER_AIOUT2 A2

#define VIN_PIN A5

#include "wiring_private.h"

void analogWrite2(uint32_t pin, uint32_t value);

class A4955Bridge {
  private:
    int in1;
    int in2;
    int vref;
    int ocln;
    int aiout;

    int vref_value;

  public:
    A4955Bridge(int in1, int in2, int vref, int ocln, int aiout)
      : in1(in1), in2(in2), vref(vref), ocln(ocln), aiout(aiout) {
      pinMode(in1, OUTPUT);
      pinMode(in2, OUTPUT);
      pinMode(vref, OUTPUT);
      pinMode(ocln, INPUT);
      pinMode(aiout, INPUT);
      setCurrent(0.5); // default max. current
    }

    void setOut(boolean in1H, boolean in2H) {
      digitalWrite(in1, in1H);
      digitalWrite(in2, in2H);
    }

    void setCurrent(float current) {
      vref_value = map((long)(current*1000.), 0, 14000, 0, 255);
      // we could write a maximum of 14A
      analogWrite2(vref, vref_value);  
    }

    float readCurrent() {
      // TODO: test
      return map(analogRead(aiout), 0, 1023, 0, 66) / 1000.;
    }

    int readOCL() {
      return digitalRead(ocln) == 0;
    }

    void printToSerial() {
      SerialUSB.print("IN1=");
      SerialUSB.print(digitalRead(in1));
      
      SerialUSB.print(", IN2=");
      SerialUSB.print(digitalRead(in2));

      SerialUSB.print(", AREF=");
      SerialUSB.print(map(vref_value, 0, 255, 0, 14000) / 1000.);
      SerialUSB.print("A");

      SerialUSB.print(", OCL=");
      SerialUSB.print(readOCL());

      SerialUSB.print(", AOUT=");
      SerialUSB.print(readCurrent());
      SerialUSB.print("A");

      SerialUSB.println();
    }
};

static int _writeResolution = 8;

// Wait for synchronization of registers between the clock domains
static __inline__ void syncDAC() __attribute__((always_inline, unused));
static void syncDAC() {
  while (DAC->STATUS.bit.SYNCBUSY == 1)
    ;
}

// Wait for synchronization of registers between the clock domains
static __inline__ void syncTC_8(Tc* TCx) __attribute__((always_inline, unused));
static void syncTC_8(Tc* TCx) {
  while (TCx->COUNT8.STATUS.bit.SYNCBUSY);
}

// Wait for synchronization of registers between the clock domains
static __inline__ void syncTCC(Tcc* TCCx) __attribute__((always_inline, unused));
static void syncTCC(Tcc* TCCx) {
  while (TCCx->SYNCBUSY.reg & TCC_SYNCBUSY_MASK);
}

static inline uint32_t mapResolution(uint32_t value, uint32_t from, uint32_t to)
{
  if (from == to) {
    return value;
  }
  if (from > to) {
    return value >> (from-to);
  }
  return value << (to-from);
}

// Right now, PWM output only works on the pins with
// hardware support.  These are defined in the appropriate
// pins_*.c file.  For the rest of the pins, we default
// to digital output.
void analogWrite2(uint32_t pin, uint32_t value)
{
  PinDescription pinDesc = g_APinDescription[pin];
  uint32_t attr = pinDesc.ulPinAttribute;

  if ((attr & PIN_ATTR_ANALOG) == PIN_ATTR_ANALOG)
  {
    // DAC handling code

    if (pin != PIN_A0) { // Only 1 DAC on A0 (PA02)
      return;
    }

    value = mapResolution(value, _writeResolution, 10);

    syncDAC();
    DAC->DATA.reg = value & 0x3FF;  // DAC on 10 bits.
    syncDAC();
    DAC->CTRLA.bit.ENABLE = 0x01;     // Enable DAC
    syncDAC();
    return;
  }

  if ((attr & PIN_ATTR_PWM) == PIN_ATTR_PWM)
  {
    value = mapResolution(value, _writeResolution, 8);

    uint32_t tcNum = GetTCNumber(pinDesc.ulPWMChannel);
    uint8_t tcChannel = GetTCChannelNumber(pinDesc.ulPWMChannel);
    static bool tcEnabled[TCC_INST_NUM+TC_INST_NUM];

    if (attr & PIN_ATTR_TIMER) {
      #if !(ARDUINO_SAMD_VARIANT_COMPLIANCE >= 10603)
      // Compatibility for cores based on SAMD core <=1.6.2
      if (pinDesc.ulPinType == PIO_TIMER_ALT) {
        pinPeripheral(pin, PIO_TIMER_ALT);
      } else
      #endif
      {
        pinPeripheral(pin, PIO_TIMER);
      }
    } else {
      // We suppose that attr has PIN_ATTR_TIMER_ALT bit set...
      pinPeripheral(pin, PIO_TIMER_ALT);
    }

    if (!tcEnabled[tcNum]) {
      tcEnabled[tcNum] = true;

      uint16_t GCLK_CLKCTRL_IDs[] = {
        GCLK_CLKCTRL_ID(GCM_TCC0_TCC1), // TCC0
        GCLK_CLKCTRL_ID(GCM_TCC0_TCC1), // TCC1
        GCLK_CLKCTRL_ID(GCM_TCC2_TC3),  // TCC2
        GCLK_CLKCTRL_ID(GCM_TCC2_TC3),  // TC3
        GCLK_CLKCTRL_ID(GCM_TC4_TC5),   // TC4
        GCLK_CLKCTRL_ID(GCM_TC4_TC5),   // TC5
        GCLK_CLKCTRL_ID(GCM_TC6_TC7),   // TC6
        GCLK_CLKCTRL_ID(GCM_TC6_TC7),   // TC7
      };
      GCLK->CLKCTRL.reg = (uint16_t) (GCLK_CLKCTRL_CLKEN | GCLK_CLKCTRL_GEN_GCLK0 | GCLK_CLKCTRL_IDs[tcNum]);
      while (GCLK->STATUS.bit.SYNCBUSY == 1);

      // Set PORT
      if (tcNum >= TCC_INST_NUM) {
        // -- Configure TC
        Tc* TCx = (Tc*) GetTC(pinDesc.ulPWMChannel);
        // Disable TCx
        TCx->COUNT8.CTRLA.bit.ENABLE = 0;
        syncTC_8(TCx);
        // Set Timer counter Mode to 8 bits, normal PWM, prescaler 1/256
        TCx->COUNT8.CTRLA.reg |= TC_CTRLA_MODE_COUNT8 | TC_CTRLA_WAVEGEN_NPWM | TC_CTRLA_PRESCALER_DIV4;
        syncTC_8(TCx);
        // Set the initial value
        TCx->COUNT8.CC[tcChannel].reg = (uint8_t) value;
        syncTC_8(TCx);
        // Set PER to maximum counter value (resolution : 0xFF)
        TCx->COUNT8.PER.reg = 0xFF;
        syncTC_8(TCx);
        // Enable TCx
        TCx->COUNT8.CTRLA.bit.ENABLE = 1;
        syncTC_8(TCx);
      } else {
        // -- Configure TCC
        Tcc* TCCx = (Tcc*) GetTC(pinDesc.ulPWMChannel);
        // Disable TCCx
        TCCx->CTRLA.bit.ENABLE = 0;
        syncTCC(TCCx);
        // Set prescaler to 1/256
        TCCx->CTRLA.reg |= TCC_CTRLA_PRESCALER_DIV4;
        syncTCC(TCCx);
        // Set TCx as normal PWM
        TCCx->WAVE.reg |= TCC_WAVE_WAVEGEN_NPWM;
        syncTCC(TCCx);
        // Set the initial value
        TCCx->CC[tcChannel].reg = (uint32_t) value;
        syncTCC(TCCx);
        // Set PER to maximum counter value (resolution : 0xFF)
        TCCx->PER.reg = 0xFF;
        syncTCC(TCCx);
        // Enable TCCx
        TCCx->CTRLA.bit.ENABLE = 1;
        syncTCC(TCCx);
      }
    } else {
      if (tcNum >= TCC_INST_NUM) {
        Tc* TCx = (Tc*) GetTC(pinDesc.ulPWMChannel);
        TCx->COUNT8.CC[tcChannel].reg = (uint8_t) value;
        syncTC_8(TCx);
    } else {
        Tcc* TCCx = (Tcc*) GetTC(pinDesc.ulPWMChannel);
        TCCx->CTRLBSET.bit.LUPD = 1;
        syncTCC(TCCx);
        TCCx->CCB[tcChannel].reg = (uint32_t) value;
        syncTCC(TCCx);
        TCCx->CTRLBCLR.bit.LUPD = 1;
        syncTCC(TCCx);
      }
    }
    return;
  }

  // -- Defaults to digital write
  pinMode(pin, OUTPUT);
  value = mapResolution(value, _writeResolution, 8);
  if (value < 128) {
    digitalWrite(pin, LOW);
  } else {
    digitalWrite(pin, HIGH);
  }
}

static A4955Bridge driver1 (DRIVER_IN1, DRIVER_IN2, DRIVER_VREF1, DRIVER_OCLn1, DRIVER_AIOUT1);
static A4955Bridge driver2 (DRIVER_IN3, DRIVER_IN4, DRIVER_VREF2, DRIVER_OCLn2, DRIVER_AIOUT2);

float readInputVoltage() {
  return map(analogRead(VIN_PIN), 0, 1023, 0, 75999) / 1000.;
}

void printStatus() {
  SerialUSB.print("VIN: ");
  SerialUSB.print(readInputVoltage());
  SerialUSB.println("V");
  
  SerialUSB.print("driver1: ");
  driver1.printToSerial();

  SerialUSB.print("driver2: ");
  driver2.printToSerial();
}

void setup() {
  SerialUSB.begin(115200);
  pinMode(LED_BUILTIN, OUTPUT);
  pinMode(VIN_PIN, INPUT);
  
  digitalWrite(LED_BUILTIN, HIGH);

  // put your main code here, to run repeatedly:
  driver1.setOut(LOW, LOW);
  driver2.setOut(LOW, LOW);
}

static int state = 0;

void loop() {
  delay(1000);
  digitalWrite(LED_BUILTIN, digitalRead(LED_BUILTIN) == LOW);

  switch(state) {
    case 0:
      driver1.setOut(LOW, HIGH);
      driver2.setOut(LOW, LOW);
      break;
      
    case 1:
      driver1.setOut(LOW, HIGH);
      driver2.setOut(LOW, HIGH);
      break;
      
    case 2:
      driver1.setOut(LOW, LOW);
      driver2.setOut(LOW, HIGH);
      break;
      
    case 3:
      driver1.setOut(HIGH, LOW);
      driver2.setOut(LOW, HIGH);
      break;
      
    case 4:
      driver1.setOut(HIGH, LOW);
      driver2.setOut(LOW, LOW);
      break;
      
    case 5:
      driver1.setOut(HIGH, LOW);
      driver2.setOut(HIGH, LOW);
      break;

    case 6:
      driver1.setOut(LOW, LOW);
      driver2.setOut(HIGH, LOW);
      break;

    case 7:
      driver1.setOut(LOW, HIGH);
      driver2.setOut(HIGH, LOW);
      break;

    case 8:
      // break
      driver1.setOut(HIGH, HIGH);
      driver2.setOut(HIGH, HIGH);
      break;

    default:
      // coast (Sleep)
      driver1.setOut(LOW, LOW);
      driver2.setOut(LOW, LOW);
      break;
        
  }

  state ++;
  if(state > 7) {
    state = 0;
  }

  delay(10);

  printStatus();
}

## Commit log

2016-10-22 Initial version of HighPower-Mechaduino schematic
    [Arduino_Zero_Base.sch, Dual_PWM_Bridge.sch, HighPower-Mechaduino.kicad_pcb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]
2016-10-22 Fix some assignment problems because of wrong library/component names
    [HighPower-Mechaduino.sch, Protected_USB_Supply.sch]
2016-10-22 Place some components onto the PCB
    [HighPower-Mechaduino.kicad_pcb, HighPower-Mechaduino.sch, PWM_Bridge_A4955.sch]
2016-10-23 Export schematic as pdf, close #2
2016-10-24 Place remaining components onto pcb, remove galvanic protection circuit
    [HighPower-Mechaduino.kicad_pcb, PoStep25-32_galvanic.sch]
2016-10-24 First routing try (don't get it as serious design!) Some initial routing so we can check where the design needs improvement
    Problems found:
    * Stepper Drivers should probably be turned, so the driver ic's can be placed on the outside of the pcb
    * rewire arm controller and or place it on the bottom layer
    * think about how to get enough current to the drivers, without disturbing the magnetic sensor
    [HighPower-Mechaduino.kicad_pcb]
2016-10-28 Improve driver part of PCB I think I improved the Driver part of the PCB quit a bit by rearanging all of the components. But there are still many points which have to be worked on. This is still only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
    [HighPower-Mechaduino.kicad_pcb, HighPower-Mechaduino.sch]
2016-10-29 Improve pcb routing, add testpoints and etc. The design improves a lot. Still lots to do, but most important design parts should now be drafted almost complete.
    [Arduino_Zero_Base.sch, HighPower-Mechaduino.kicad_pcb, HighPower-Mechaduino.sch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]
2016-11-05 Improve pcb
    [HighPower-Mechaduino.kicad_pcb, HighPower-Mechaduino.sch]
2016-11-05 Improve board routing, add some dukos
    [HighPower-Mechaduino.kicad_pcb, HighPower-Mechaduino.sch, MCP16331_5V.sch]
2016-11-05 Add oval mounting holes to support NEMA23 as well as NEMA24
    [HighPower-Mechaduino.kicad_pcb, HighPower-Mechaduino.sch]
2016-11-05 Improve Edge cuts
    [HighPower-Mechaduino.kicad_pcb]
2016-11-05 Move processor part a bit down
    [HighPower-Mechaduino.kicad_pcb, HighPower-Mechaduino.sch, PWM_Bridge_A4955.sch]
2016-11-05 Add some little changes to the schematic, add calculations
    [Arduino_Zero_Base.sch, HighPower-Mechaduino.kicad_pcb, HighPower-Mechaduino.sch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]
2016-11-15 Add some digikey order informations to components
    [Arduino_Zero_Base.sch, HighPower-Mechaduino.sch, MCP16331_5V.sch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]
2016-11-15 Add more order informations, create BOM
    [HighPower-Mechaduino.sch, PWM_Bridge_A4955.sch, PoStep25-32_galvanic.sch]
2016-11-15 Add link to current BOM
2016-11-15 Add more BOM informations
    [Arduino_Zero_Base.sch, HighPower-Mechaduino.sch, MCP16331_5V.sch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]
2016-11-15 Improve BOM
    [Arduino_Zero_Base.sch, HighPower-Mechaduino.sch, MCP16331_5V.sch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]
2016-11-17 Use new library symbols
    [Arduino_Zero_Base.sch, HighPower-Mechaduino.kicad_pcb, HighPower-Mechaduino.sch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]
2016-11-19 Improve pcb routing
    [HighPower-Mechaduino.kicad_pcb, MCP16331_5V.sch, PWM_Bridge_A4955.sch]
2016-11-19 Improve layout and add voltage sensing circuit to layout
    [Arduino_Zero_Base.sch, HighPower-Mechaduino.kicad_pcb, HighPower-Mechaduino.sch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]
2016-11-19 Fix inductor (old one was no longer available)
    [HighPower-Mechaduino.kicad_pcb, MCP16331_5V.sch]
2016-11-19 Add Fiducials to pcb
    [HighPower-Mechaduino.kicad_pcb]
2016-11-26 Add some improvements, fix issue with schematic error
    [Arduino_Zero_Base.sch, HighPower-Mechaduino.kicad_pcb, HighPower-Mechaduino.sch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]
2016-11-26 Improve pcb (add more part dimensions on the F.Fab layer)
    [HighPower-Mechaduino.kicad_pcb]
2016-11-26 Fix little schematic error
    [HighPower-Mechaduino.kicad_pcb, HighPower-Mechaduino.sch, PWM_Bridge_A4955.sch]
2016-11-26 update mounting hole symbol
    [Arduino_Zero_Base.sch, HighPower-Mechaduino.kicad_pcb, HighPower-Mechaduino.sch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]
2016-11-26 Add OSHW and KiCad logo
    [HighPower-Mechaduino.kicad_pcb]
2016-11-29 Improve pcb layout
    [HighPower-Mechaduino.kicad_pcb, HighPower-Mechaduino.sch, MCP16331_5V.sch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]
2016-12-01 Add Digital IO connector
    [Arduino_Zero_Base.sch, HighPower-Mechaduino.kicad_pcb, HighPower-Mechaduino.sch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]
2016-12-01 Fix connector footprint
    [HighPower-Mechaduino.kicad_pcb, PoStep25-32_galvanic.sch]
2016-12-03 Remove connection to SLEEPn Pin
    I think we don't have to connect this pin, and if yes we can fix it manually on the prototype
    The support of Alegro wasn't very helpful about that topic
    [HighPower-Mechaduino.kicad_pcb, HighPower-Mechaduino.sch, PWM_Bridge_A4955.sch]
2016-12-03 Add Text to pcb
    [HighPower-Mechaduino.kicad_pcb]
2016-12-03 Update Capacitors
    [HighPower-Mechaduino.kicad_pcb, MCP16331_5V.sch, PWM_Bridge_A4955.sch]
2016-12-03 Some little improvements
    [Arduino_Zero_Base.sch, HighPower-Mechaduino.kicad_pcb, HighPower-Mechaduino.sch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]
2016-12-03 Update BOM
2016-12-08 Fix #5
    [HighPower-Mechaduino.kicad_pcb, PWM_Bridge_A4955.sch]
2016-12-08 Fix #7
    [HighPower-Mechaduino.kicad_pcb, HighPower-Mechaduino.sch]
2016-12-08 Fix schematic error described in #8
    [Arduino_Zero_Base.sch, HighPower-Mechaduino.kicad_pcb, HighPower-Mechaduino.sch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]
2016-12-17 Update schematic
    [HighPower-Mechaduino.kicad_pcb, MCP16331_5V.sch]
2016-12-20 Little update
    [HighPower-Mechaduino.sch, PWM_Bridge_A4955.sch]
2017-01-07 Fix #13
    [Arduino_Zero_Base.sch, HighPower-Mechaduino.kicad_pcb, HighPower-Mechaduino.sch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]
2017-02-04 Increase hole size to be compatible to M5
    [HighPower-Mechaduino.kicad_pcb]
2017-02-04 Improve grounding of motor controller (for shunt measurement), Fix #4
    [HighPower-Mechaduino.kicad_pcb]
2017-02-04 Some little cleanups
    [Arduino_Zero_Base.sch, HighPower-Mechaduino.kicad_pcb, HighPower-Mechaduino.sch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]
2017-02-11 Some changes to the step down converter, Fix #8
    [Arduino_Zero_Base.sch, HighPower-Mechaduino.kicad_pcb, HighPower-Mechaduino.sch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]
2017-02-18 Improve schematic and pcb (add snubber network to driver output)
    [Arduino_Zero_Base.sch, HighPower-Mechaduino.kicad_pcb, HighPower-Mechaduino.sch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]
